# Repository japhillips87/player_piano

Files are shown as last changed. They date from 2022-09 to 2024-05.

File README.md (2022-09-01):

# player_piano

This project is a DIY piano player. It is still a work in progress.

To make this project run, you will need to install a few libraries. First, you will need to install the ESP32 in the Arduino IDE. You can do that by following [this guide](https://randomnerdtutorials.com/installing-the-esp32-board-in-arduino-ide-windows-instructions/).

Then you will need to search for a few libraries to install in the IDE. The first is [Arduino-BLE-MIDI](https://github.com/lathoub/Arduino-BLE-MIDI). If you install
this through the Arduino IDE, you don't need to install the midi library. But if you don't install it through the IDE, you need to install it from [here](https://github.com/FortySevenEffects/arduino_midi_library). And finally, you need the [PCA9635](https://github.com/RobTillaart/PCA9635) library.

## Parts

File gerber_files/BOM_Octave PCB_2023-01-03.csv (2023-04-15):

ID | Name | Designator | Footprint | Quantity | Manufacturer Part | Manufacturer | Supplier | Supplier Part | Price
1 | jumper | A0,A1,A2,A3,A4,A5 | JUMPER_SOLDER_1X2 | 6
2 | 1200uF | C2 | CAP-TH_BD10.0-P5.00-D0.6-FD | 1 | UPW1C122MPD | Nichicon(尼吉康) | LCSC | C445354 | 0.063
3 | HDR-M-2.54_1x4 | J8,J9 | HDR-M-2.54_1X4 | 2 |  |  | LCSC | C124378 | 0.007
4 | DB127V-5.0-8P-GN-S | U1,U3,U4,U5 | CONN-TH_8P-P5.00_DIBO_DB127V-5.0-8P-GN-S | 4 | DB127V-5.0-8P-GN-S | DIBO | LCSC | C430626 | 0.07
5 | 10uF | C1 | C0603 | 1 | LMK107BJ106MALTD | TAIYO YUDEN | LCSC | C18800 | 0.002
6 | BYQ28E-200,127 | D1,D2,D3,D4,D5,D7,D8,D9,D10,D11,D12,D13,D14,D15,D16,D6 | TO-220-3_L10.0-W4.5-P2.54-L | 16 | BYQ28E-200,127 | WeEn Semiconductors | LCSC | C128814 | 0.056
7 | IRL520NPBF | Q1,Q2,Q3,Q4,Q5,Q7,Q8,Q9,Q10,Q11,Q12,Q13,Q14,Q15,Q16,Q6 | TO-220AB-3_L10.4-W4.5-P2.54-L | 16 | IRL520NPBF | Infineon(英飞凌) | LCSC | C538129 | 0.14
8 | 10K | R1,R2 | R0603 | 2 | AC0603FR-0710KL | YAGEO | LCSC | C116677
9 | 220Ω | RN1,RN2,RN3,RN4 | RES-ARRAY-SMD_0603-8P-L3.2-W1.6-BL | 4 | 4D03WGJ0221T5E | UniOhm | LCSC | C29719 | 0.001
10 | 10K | RN5,RN6 | RES-ARRAY-SMD_0603-8P-L3.2-W1.6-BL | 2 | YC164-JR-0710KL | YAGEO | LCSC | C107374 | 0.001
11 | PCA9635PW,118 | PCA9635 | TSSOP-28_L9.7-W4.4-P0.65-LS6.4-BL | 1 | PCA9635PW,118 | NXP | LCSC | C110795 | 0.316
12 | XT30U-M SM | J7 | XT30U-M | 1 |  | Changzhou Amass Electronics CO.LTD.
13 | CONN_XT30U-F | CONN1 | CONN_XT30U | 1

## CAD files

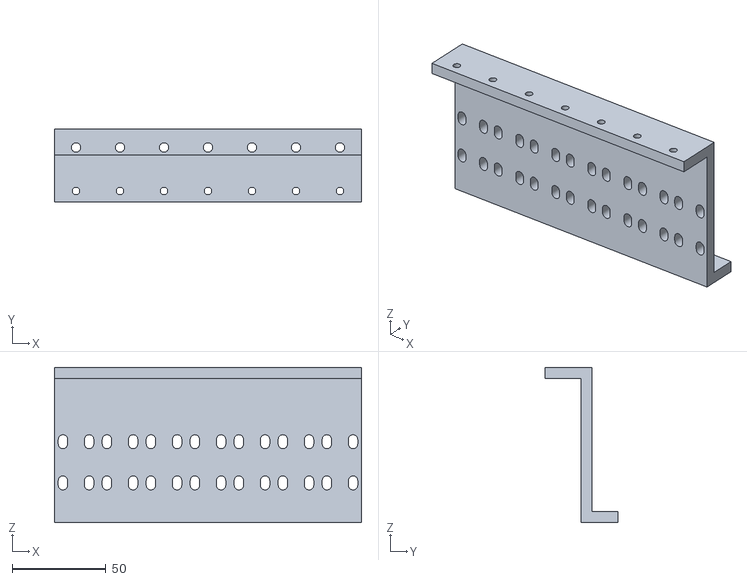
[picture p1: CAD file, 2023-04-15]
stl_files/white_key_octave_corrected.stl
164.0 x 39.2 x 83.0

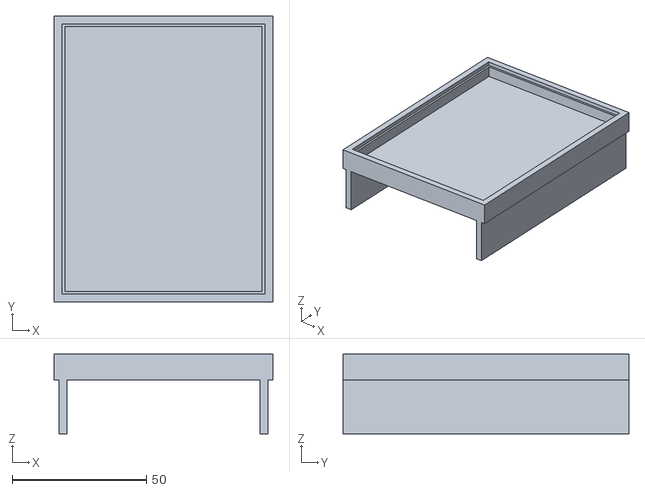
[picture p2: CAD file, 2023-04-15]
stl_files/driver_board_holder.stl
81.5 x 106.5 x 29.8

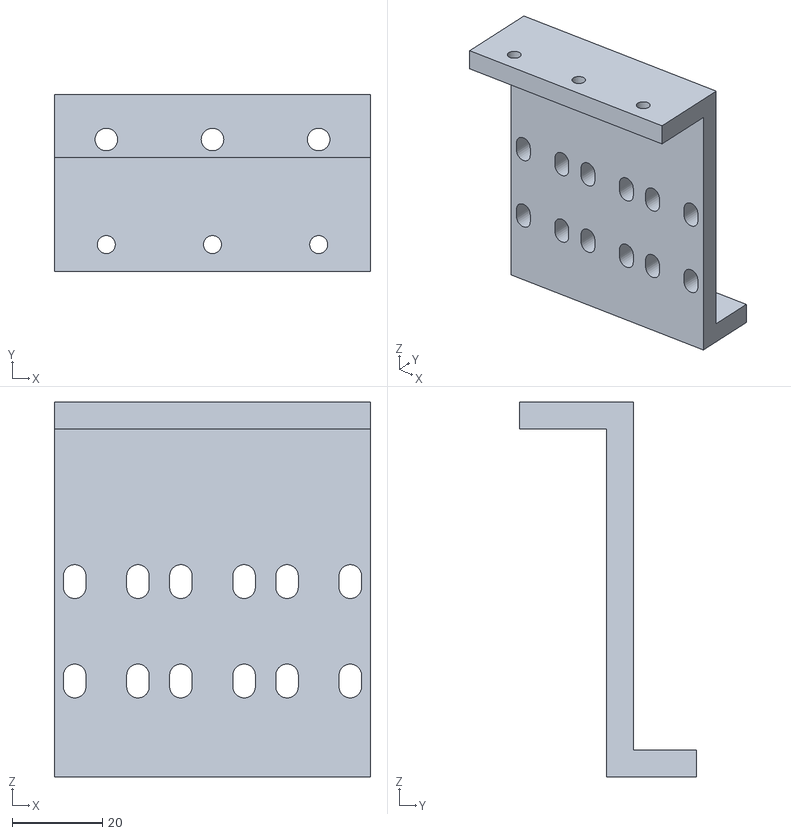
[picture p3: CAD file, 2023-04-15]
stl_files/three_key_corrected.stl
70.0 x 39.2 x 83.0

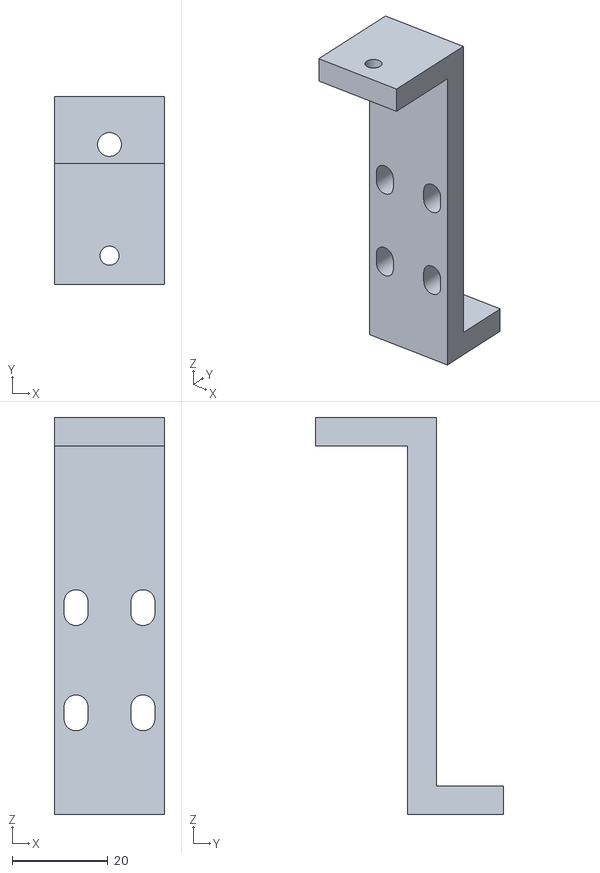
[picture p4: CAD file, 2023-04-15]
stl_files/single_key_corrected.stl
23.0 x 39.2 x 83.0

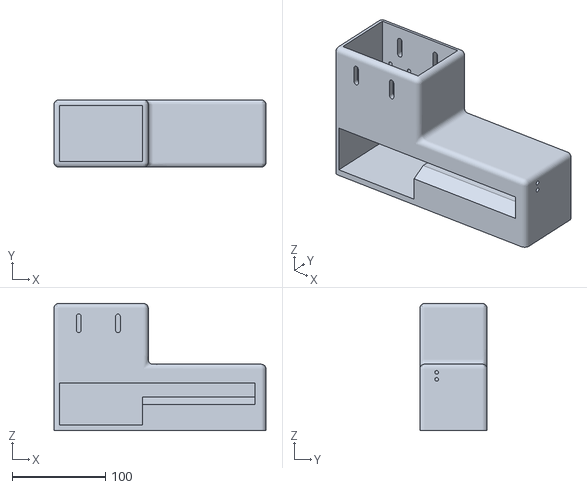
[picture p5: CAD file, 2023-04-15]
stl_files/housing_body_v6.stl
227.0 x 72.0 x 136.0

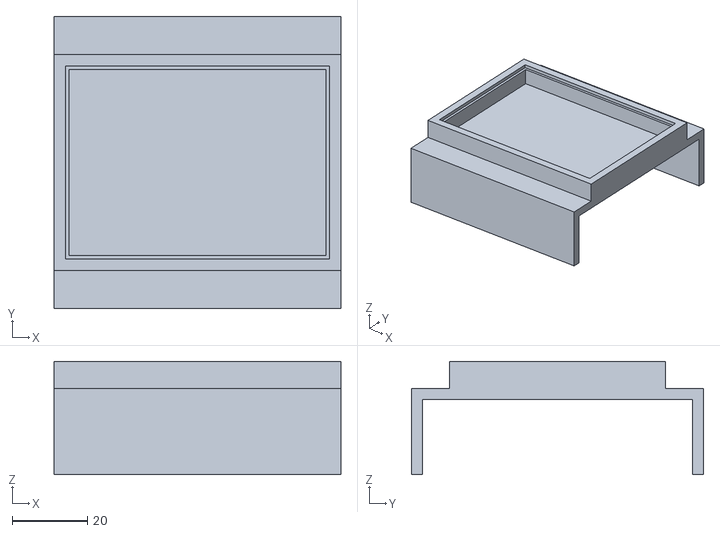
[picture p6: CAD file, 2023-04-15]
stl_files/esp_board_holder.stl
76.5 x 77.9 x 30.2

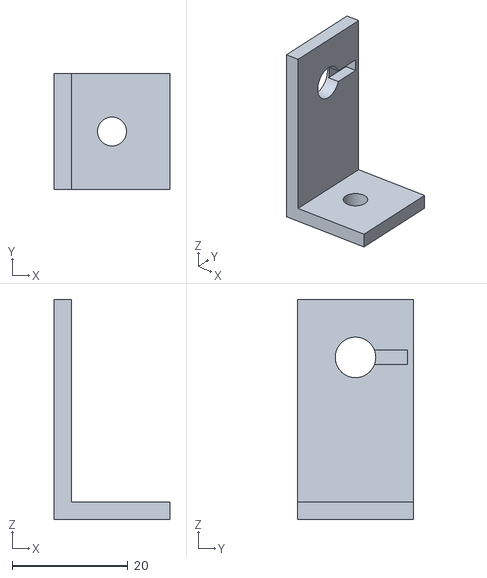
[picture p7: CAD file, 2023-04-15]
stl_files/volume_pot_mount.stl
20.0 x 20.0 x 38.0

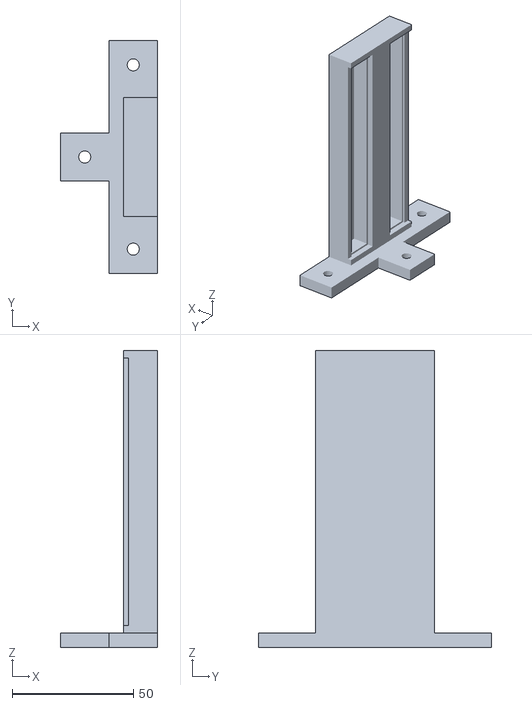
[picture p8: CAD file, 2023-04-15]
stl_files/bus_bar_holder.stl
40.0 x 96.0 x 122.5

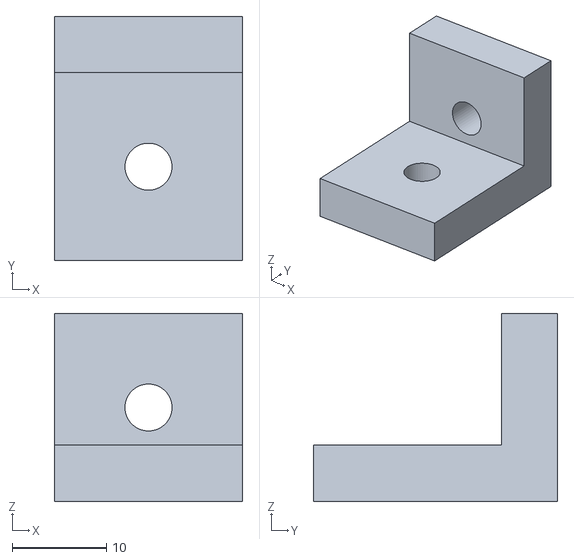
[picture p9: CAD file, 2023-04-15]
stl_files/2020_90_degree_bracket_offset.stl
20.0 x 26.0 x 20.0

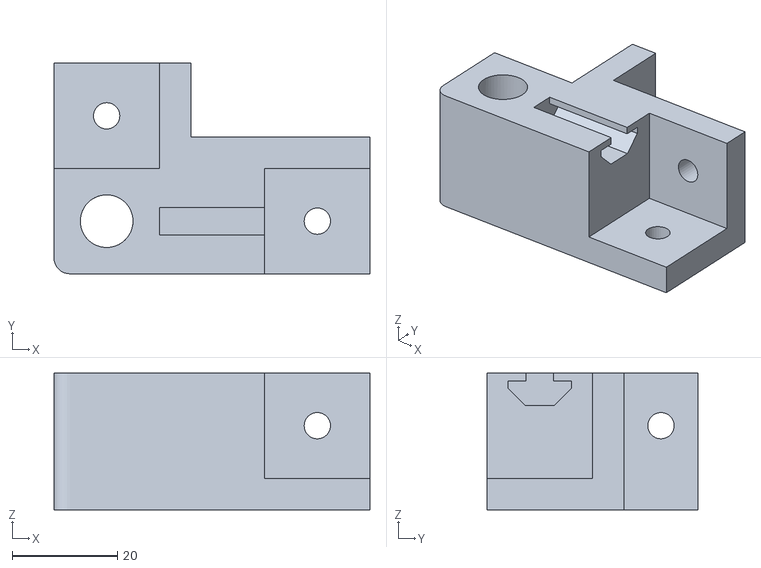
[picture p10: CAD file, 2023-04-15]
stl_files/2020_corner_v2.stl
60.0 x 40.0 x 26.0

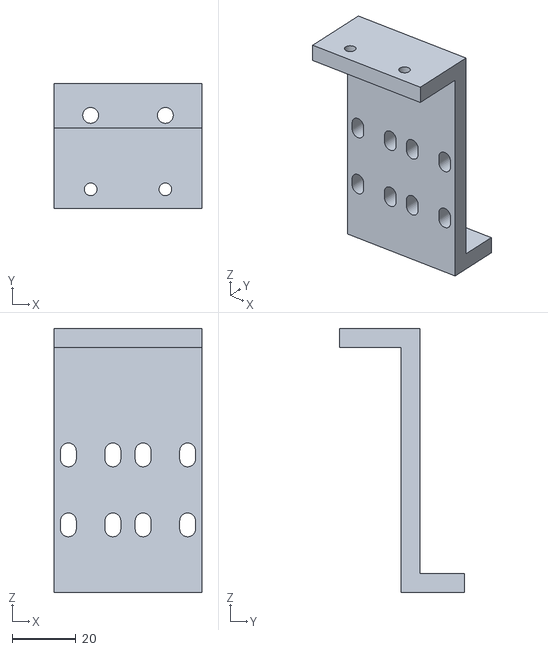
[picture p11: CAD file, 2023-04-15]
stl_files/two_key_corrected.stl
46.5 x 39.2 x 83.0

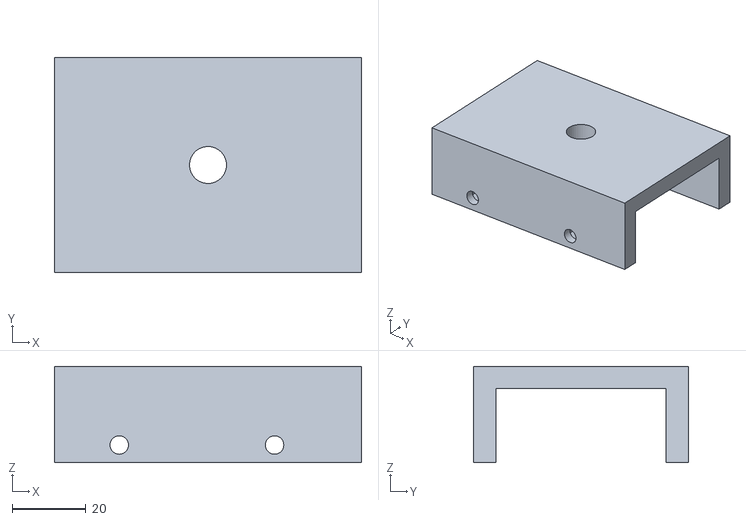
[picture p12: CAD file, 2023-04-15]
stl_files/top_lid_v2.stl
83.0 x 58.0 x 26.0

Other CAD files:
fusion360_files/2020_brackets.f3d
fusion360_files/Pedal Solenoid Holder.f3d
fusion360_files/bus_bar_holder.f3d
fusion360_files/driver_board_holder.f3d
fusion360_files/esp_board_holder.f3d
fusion360_files/solenoid_holders_v2.f3d
fusion360_files/volume_pot_mount.f3d

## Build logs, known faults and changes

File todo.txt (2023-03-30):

notes needs to use NoteSchedule
schedule can be deleted (after borrowing some of the code)
commands needs to be moved to the piano

loop method changes:
  - loop through notes and check the schedule
    - within checkSchedule() see if notes can be played as is or if they need
      to be modified
    - if they need to be modified, do it and add to commands
    - if they can be played as is, add to commands
    - if there is nothing to do, move on with no-op
  - loop through piano commands
    - play commands at specified time

MIDI callback changes:
  - handle note on callback through the piano
    - something like piano.handleNoteOn(midiId, velocity)
      - the handleNoteOn method will be responsible for looking up note and
        adding the correct info to the noteSchedule

processSchedule:
  - if there is no schedule
    - no-op
  - else if the delay has been reached
    - command the note
  - else
    - if there is only one scheduled event
      - no-op
    - else
      - check the first two scheduled events
        - if they have enough time
          - no-op
        - else
          - figure out what needs to be changed and command the note for the proper time

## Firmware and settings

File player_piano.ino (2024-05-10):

#include <BLEMIDI_Transport.h>
#include <hardware/BLEMIDI_ESP32_NimBLE.h>
#include "piano.h"
#include "sustain.h"
#include "command.h"
#include "PCA9635.h"
#include <stdint.h>

Piano piano;
Sustain sustain;

PCA9635 board1(0x40);
PCA9635 board2(0x41);
PCA9635 board3(0x42);
PCA9635 board4(0x43);
PCA9635 board5(0x44);
PCA9635 board6(0x45);
PCA9635 board7(0x46);

BLEMIDI_CREATE_INSTANCE("Amadeus", MIDI)

void setup() {
  Serial.begin(115200);
  MIDI.begin(MIDI_CHANNEL_OMNI);

//  BLEMIDI.setHandleConnected([]() { schedule.connected(); });
//  BLEMIDI.setHandleDisconnected([]() { schedule.disconnected(); });

  piano.initialize();
//  schedule.poweredOn();

  // UPDATE: this needs to use the addToSchedule function
  MIDI.setHandleNoteOn([](uint8_t _, uint8_t noteId, uint8_t velocity) { piano.scheduleNote(noteId, velocity); });
  MIDI.setHandleNoteOff([](uint8_t _, uint8_t noteId, uint8_t velocity) { piano.scheduleNote(noteId, 0); });
  MIDI.setHandleControlChange([](uint8_t channel, uint8_t number, uint8_t value) { piano.scheduleSustain(channel, number, value); });
  
  Wire.begin(SDA_PIN, SCL_PIN);
  
  board1.begin(PCA9635_MODE1_NONE, PCA9635_MODE2_INVERT | PCA9635_MODE2_TOTEMPOLE);
  for (int channel = 0; channel < board1.channelCount(); channel++) {
    board1.setLedDriverMode(channel, PCA9635_LEDPWM);
    board1.write1(channel, 0);
  }
  board2.begin(PCA9635_MODE1_NONE, PCA9635_MODE2_INVERT | PCA9635_MODE2_TOTEMPOLE);
  for (int channel = 0; channel < board2.channelCount(); channel++) {
    board2.setLedDriverMode(channel, PCA9635_LEDPWM);
    board2.write1(channel, 0);
  }
  board3.begin(PCA9635_MODE1_NONE, PCA9635_MODE2_INVERT | PCA9635_MODE2_TOTEMPOLE);
  for (int channel = 0; channel < board3.channelCount(); channel++) {
    board3.setLedDriverMode(channel, PCA9635_LEDPWM);
    board3.write1(channel, 0);
  }
  board4.begin(PCA9635_MODE1_NONE, PCA9635_MODE2_INVERT | PCA9635_MODE2_TOTEMPOLE);
  for (int channel = 0; channel < board4.channelCount(); channel++) {
    board4.setLedDriverMode(channel, PCA9635_LEDPWM);
    board4.write1(channel, 0);
  }
  board5.begin(PCA9635_MODE1_NONE, PCA9635_MODE2_INVERT | PCA9635_MODE2_TOTEMPOLE);
  for (int channel = 0; channel < board5.channelCount(); channel++) {
    board5.setLedDriverMode(channel, PCA9635_LEDPWM);
    board5.write1(channel, 0);
  }
  board6.begin(PCA9635_MODE1_NONE, PCA9635_MODE2_INVERT | PCA9635_MODE2_TOTEMPOLE);
  for (int channel = 0; channel < board6.channelCount(); channel++) {
    board6.setLedDriverMode(channel, PCA9635_LEDPWM);
    board6.write1(channel, 0);
  }
  board7.begin(PCA9635_MODE1_NONE, PCA9635_MODE2_INVERT | PCA9635_MODE2_TOTEMPOLE);
  for (int channel = 0; channel < board7.channelCount(); channel++) {
    board7.setLedDriverMode(channel, PCA9635_LEDPWM);
    board7.write1(channel, 0);
  }
}

void loop() {
  MIDI.read();  
  // loop through the notes and and see if their schedule needs to be adjusted
  // Serial.println("Looping through notes");
  for (auto it = piano.notes.begin(); it != piano.notes.end(); it++) {
    it->processSchedule();
    it->checkForErrors();
  }

  sustain.processSchedule();
  sustain.checkForErrors();

  // loop through the commands and find which ones need to run
  for (auto it = piano.commands.begin(); it != piano.commands.end(); it++) {
    int midiId = it->getMidiId();
    if (midiId >= BOARD_1_MIN_ID && midiId <= BOARD_1_MAX_ID) {
      board1.write1(midiId - BOARD_1_MIN_ID, it->getPwm());
    } else if (midiId >= BOARD_2_MIN_ID && midiId <= BOARD_2_MAX_ID) {
      board2.write1(midiId - BOARD_2_MIN_ID, it->getPwm());
    } else if (midiId >= BOARD_3_MIN_ID && midiId <= BOARD_3_MAX_ID) {
      board3.write1(midiId - BOARD_3_MIN_ID, it->getPwm());
    } else if (midiId >= BOARD_4_MIN_ID && midiId <= BOARD_4_MAX_ID) {
      board4.write1(midiId - BOARD_4_MIN_ID, it->getPwm());
    } else if (midiId >= BOARD_5_MIN_ID && midiId <= BOARD_5_MAX_ID) {
      board5.write1(midiId - BOARD_5_MIN_ID, it->getPwm());
    } else if (midiId >= BOARD_6_MIN_ID && midiId <= BOARD_6_MAX_ID) {
      board6.write1(midiId - BOARD_6_MIN_ID, it->getPwm());
    } else if (midiId >= BOARD_7_MIN_ID && midiId <= BOARD_7_MAX_ID) {
      board7.write1(midiId - BOARD_7_MIN_ID, it->getPwm());
    } else if (midiId == 109) { // sustain
      board7.write1(SUSTAIN_1_INDEX, it->getPwm());
      board7.write1(SUSTAIN_2_INDEX, it->getPwm());
    }
//    Serial.print("RUNNING COMMAND: ");
//    Serial.print("Midi Id: ");
//    Serial.print(it->getMidiId());
//    Serial.print(", PWM: ");
//    Serial.println(it->getPwm());
    piano.commands.erase(it--);
  }
}

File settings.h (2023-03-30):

#pragma once

const int OFF_PWM = 0;
const int ON_PWM = 255;
const int POT_PIN = 36;
//const int STARTUP_DURATION = 13;
//const int VELOCITY_DURATION = 40;
//const int TOTAL_ON_DURATION = STARTUP_DURATION + VELOCITY_DURATION;
const int NOTE_HOLD_PWM = 90;
const int NOTE_MIN_PWM = 115;
const int NOTE_MAX_PWM = 255;
const int NOTE_MID_PWM = (NOTE_MIN_PWM + NOTE_MAX_PWM) / 2;
const int MIN_MIDI_VELOCITY = 0;
const int MAX_MIDI_VELOCITY = 127;
const int MIDI_HALF_VELOCITY = (MIN_MIDI_VELOCITY + MAX_MIDI_VELOCITY) / 2;
const int SUSTAIN_THRESHOLD = 64;
const int SUSTAIN_COMMAND_ID = 109;
const int SUSTAIN_CONTROL_NUMBER = 64;
const int MIN_NOTE_ID = 21;
const int MAX_NOTE_ID = 108;
// const int SUSTAIN_STARTUP_DURATION = 30;
// const int SUSTAIN_POWER_DURATION = 100;
// const int SUSTAIN_TOTAL_ON_DURATION = SUSTAIN_STARTUP_DURATION + SUSTAIN_POWER_DURATION;
// const int SUSTAIN_VELOCITY = 127;
// const int SUSTAIN_HOLD_PWM = 50;
// const int SUSTAIN_DEACTIVATE_TIME_REQUIRED = 200;
const int SDA_PIN = 21;
const int SCL_PIN = 22;
const int MIN_STARTUP_MS     = 18;
const int MAX_STARTUP_MS     = 18;
const int VELOCITY_MS        = 45;
const int MIN_DEACTIVATE_MS  = 75;
const int MAX_DEACTIVATE_MS  = 80;
const int FAST_DEACTIVATE_MS = 52;
const int SUSTAIN_ON_MS      = 91;
const int SUSTAIN_HOLD_PWM   = 180;
const int SUSTAIN_OFF_MS     = 50;
const int NOTE_TIMEOUT_MS    = 10000;
const int SUSTAIN_TIMEOUT_MS = 30000;
const int AUTO_RESET_MS      = 360000;
// Delay Settings
const int FULL_DELAY = MAX_STARTUP_MS + VELOCITY_MS + MAX_DEACTIVATE_MS;
// BOARD_MIDI_VALUES
const int BOARD_1_MIN_ID = 21;
const int BOARD_1_MAX_ID = 35;
const int BOARD_2_MIN_ID = 36;
const int BOARD_2_MAX_ID = 47;
const int BOARD_3_MIN_ID = 48;
const int BOARD_3_MAX_ID = 59;
const int BOARD_4_MIN_ID = 60;
const int BOARD_4_MAX_ID = 71;
const int BOARD_5_MIN_ID = 72;
const int BOARD_5_MAX_ID = 83;
const int BOARD_6_MIN_ID = 84;
const int BOARD_6_MAX_ID = 95;
const int BOARD_7_MIN_ID = 96;
const int BOARD_7_MAX_ID = 108;
const int SUSTAIN_1_INDEX = 13;
const int SUSTAIN_2_INDEX = 14;
// TODO: calibrate these values
const int BLUETOOTH_SOUND_DELAY = 75;
const int BLUETOOTH_SOUND_DURATION = 300;
const int POWER_SOUND_DURATION_ONE = 200;
const int POWER_SOUND_DURATION_TWO = 1000;
const int POWER_SOUND_DELAY = 100;

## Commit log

2022-09-02 switch to vs code and add some callbacks
2022-09-02 refactor and add power on and BT sounds
2022-09-03 stub out calibration methods
2022-11-14 calibration done
2022-12-05 more code updates and stubbing out of future boards
2023-02-02 WIP - putting a pin in this for now
2023-02-02 fix last few bugs
    [note.cpp, player_piano.ino, settings.h]
2023-02-23 fixed a bug where only last board would play
    [note.cpp, player_piano.ino, settings.h]
2023-04-15 add gerber and stl files
    [2020_90_degree_bracket_offset.stl, 2020_corner_v2.stl, BOM_Octave PCB_2023-01-03.csv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]
2023-07-18 add fusion 360 files
    [Pedal Solenoid Holder.f3d, bus_bar_holder.f3d, driver_board_holder.f3d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]
2023-09-15 scaledVelocity and setHandleNoteOff
    -return scaledVelocity in note.cpp
    -velocity set to 0 in scheduleNote for NOTE OFF midi messages
